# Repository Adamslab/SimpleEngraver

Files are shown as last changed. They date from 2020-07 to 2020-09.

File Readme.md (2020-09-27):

## Simple Engraver

A simple X/Y plotter for use with a laser diode.





https://www.youtube.com/watch?v=ll7KeXLQTyo

### Printed parts:

* 2x Y-Axis Carriage
* 1x X-Axis Carriage
* 4x Feet

### BoM:

* 1x Pair of Good Laser Goggles
* 10x 5mm ID roller wheels - Either 21.5mm OD or 24mm OD
* 10x M5x30mm Bolts
* 10x M5 Nuts
* 34x M3x10mm Bolts
* 28x M3 T-Nuts
* 6x M3 Nuts
* 34x M3 Washers
* 3x 2040 Extrusion - T-Slot if using 21.5mm Wheels otherwise V-Slot for 24mm OD Wheels
* 1x GRBL Control board*
* 1x PWM Laser Diode with Heatsink
* 3x A4988 Stepper Drivers
* 3x Nema-17 Stepper Motors (Low power motors are fine)
* 1x Stepper motor splitter (To drive 2x Y-Axis motors)
* 3x 20-tooth GT2 5mm ID Motor Pulley
* 1x 5m GT2 Belt (Length required will depend on your 2040 extrusions)

You can use washers to help protect your printed parts, it's optional. 

For the 2040 extrusion, the longer the extrusions the bigger your engraving area will be. 
You can mix/match pieces or use two pieces of 2020 extrusion together to get 2040. I used 3x 500mm 2040 for my build.

There are lots of options for the control board. You can find Arduino UNO and Arduino Nano CNC shields for a very low cost. 
For my build, I used a Keyestudio KS0288. If your control board doesn't have two Y-Axis outputs, you will need a splitter.

For stepper motor drivers, I chose A4988 because I have a lot of them.
You could opt for something like DRV8255 or TMC drivers if that is more readily available.

I use software endstops, so I haven't bothered to add physical limit switches yet. 
You could always just stick some endstops on with epoxy or modify the models.

I use a 12V PWM switchable, adjustable focus laser. There is not a Z axis yet so adjustments are done manually.
Make sure the wavelength of your laser is protected by your safety glasses!

You can fasten the feet to a sheet of plywood or a table to increase rigidity of the assembly. 
Tension the belts by pulling the belt tight and tensioning the M3 bolt on top so that it bites into the belt.

https://www.thingiverse.com/thing:4556472

Adam's Lab<br>
www.adamslab.ca<br>
@adamsprints on Instagram

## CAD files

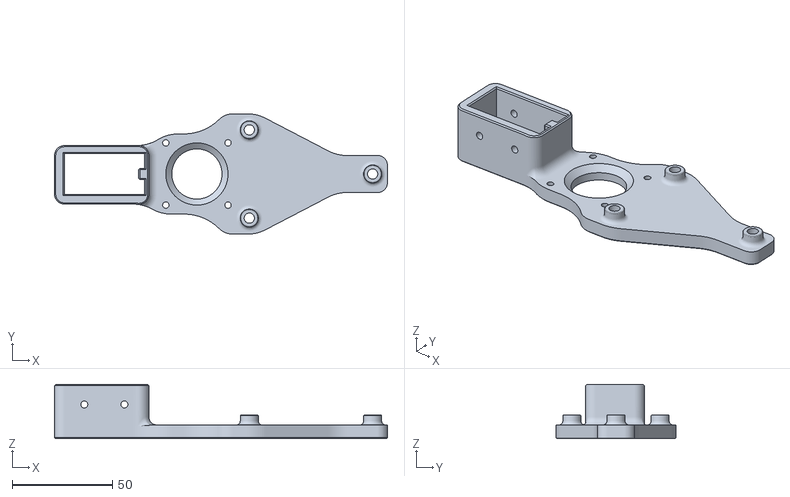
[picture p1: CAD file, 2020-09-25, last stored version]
24mm Y-Axis Carriage.stl
166.0 x 60.0 x 27.0

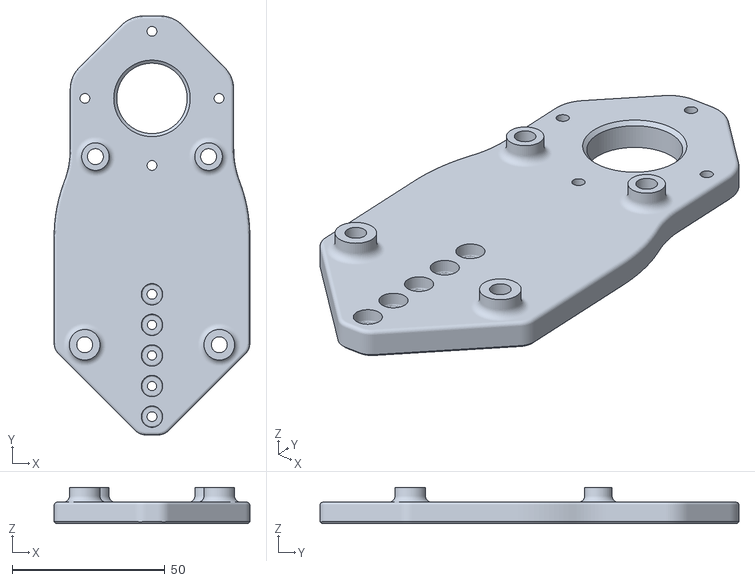
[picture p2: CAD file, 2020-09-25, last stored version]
24mm X-Axis Carriage.stl
64.0 x 137.0 x 11.8

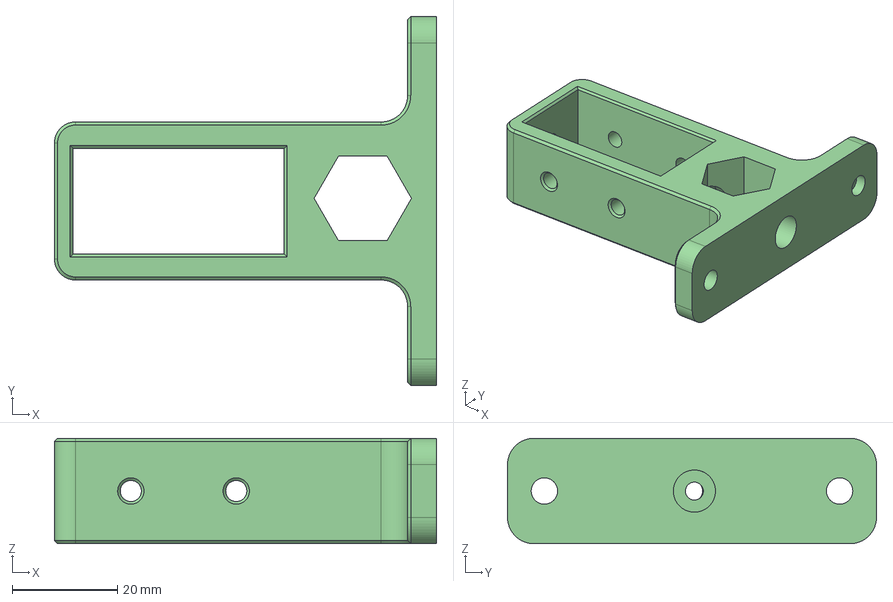
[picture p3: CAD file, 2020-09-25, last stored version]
2040 Foot.step
72.5 x 70.0 x 20.0 mm

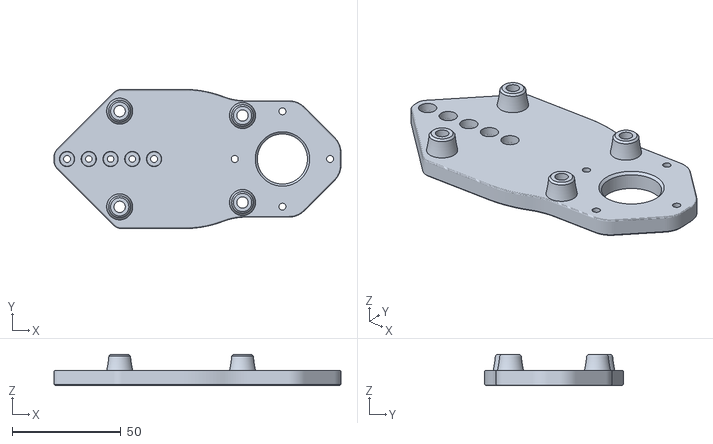
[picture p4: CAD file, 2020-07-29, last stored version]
21.5mm X-Axis Carriage.stl
132.0 x 64.0 x 14.4

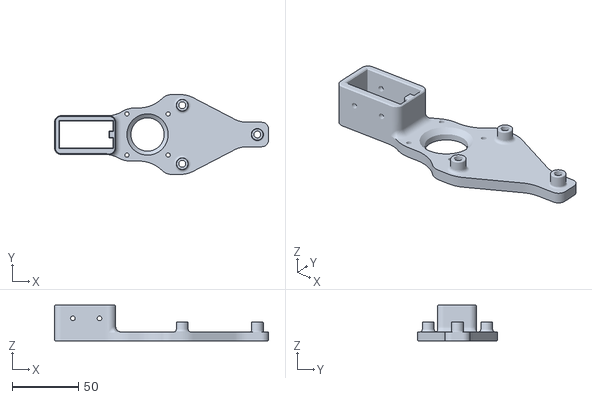
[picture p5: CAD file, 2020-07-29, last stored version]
21.5mm Y-Axis Carriage.stl
161.0 x 60.0 x 27.0

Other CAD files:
2040 Foot.stl
